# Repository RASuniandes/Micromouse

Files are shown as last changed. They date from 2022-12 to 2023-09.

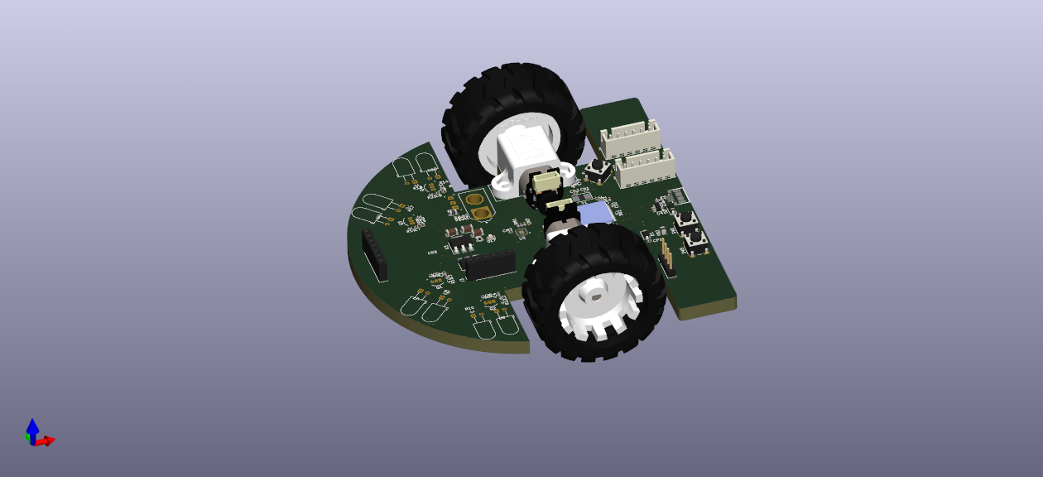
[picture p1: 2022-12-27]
Micromouse-Kicad/Micromouse-kicad.png

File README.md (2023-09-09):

<h1 align="center">RAS Uniandes  - Micromouse 🐭🧀</h1>

### The autonomous maze-solving robot:

- SoB built around the STM32F405RGT6 
  - Wall detection based on peripheral infrared sensors and ToF
  - Position and speed control using magnetic encoders for Micro Metal Motors
  - IMU aided control
  - Bluetooth support
 
- Designed using KiCad
 
- Developed in the *Universidad de Los Andes* for the *Robotics and Automation Society* Chapter of the IEEE.

## Developed by: 
<ul>
  <li>Juan Sebastián Ortega Romero(https://github.com/tadzio8425)</li>
</ul>

## To do: 
- [x] Initial research regarding the state of the art of the competition
- [x] Selection of essential components 
- [x] Initial schematic design
- [x] Altium simulations
- [x] Infrared sensors breadboard testing
- [x] Schematic revisions and corrections
- [x] PCB Design and rule check
- [x] BOM File and quote requests
- [x] Final PCB revisions
- [x] Fabrication using the services of JLCPCB
- [x] Soldering components
- [x] Unitary tests
- [x] Coding Serial, USB and Bluetooth communications
- [x] Coding sensors
- [x] Coding a general version of the FloodFill algorithm in C
- [ ] Control and PID algorithm for position and speed
- [ ] Juncture of the control algorithm and FloodFill for maze solving
- [ ] Robot calibration in a real maze
- [ ] Development of external interfaces to ease communication with the robot

## Shematic
Micromouse-kicad

## PCB Design and 3D Render

| PCB | 3D |
| --- | --- |
|  |  | 

## Robot
| Initial Assembly | Final Version |
| --- | --- |
|  |  |

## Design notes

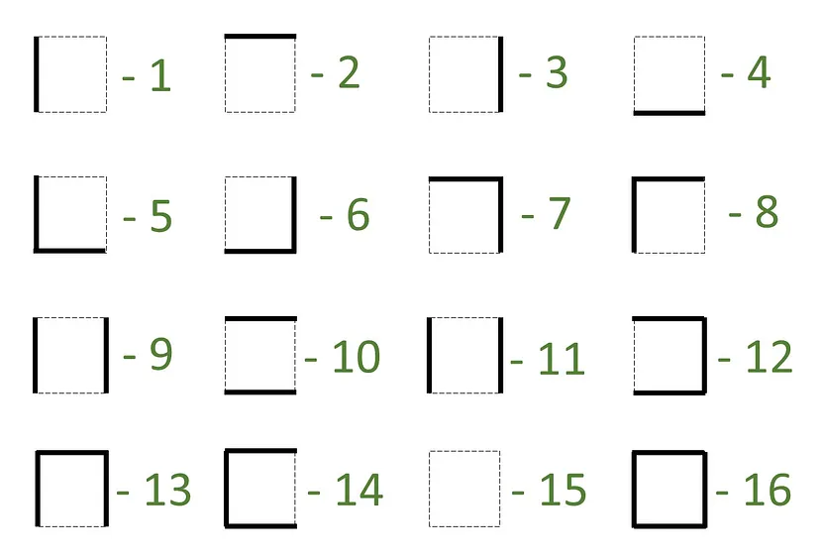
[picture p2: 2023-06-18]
Algoritmos/imgParedes.webp

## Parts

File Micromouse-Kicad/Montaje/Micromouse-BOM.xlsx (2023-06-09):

Designator | Footprint | Comment | JLCPCB Part #
RBOT1,RB2,RBOT2,RRST1,RB1 | R_0402_1005Metric | 10K | C25744
R20,R11,R19,R12 | R_0402_1005Metric | 1.5K | C25867
CRST1,CP1,CF2,CM2,CD4,CBOT1,CBOT2,CD3,CM1,CD5,CD2,CD1 | C_0402_1005Metric | 100nF | C1525
C6,CDR1,C1,C2,C5 | C_0402_1005Metric | 4.7uF | C23733
U3 | SOT-223-3_TabPin2 | AMS1117-3.3 | C6186
RU1 | R_0402_1005Metric | 1.5K | C25867
RPU1,RM1,RPU2 | R_0402_1005Metric | 4.7K | C25900
R15,R16,R8,R7,RD1 | R_0402_1005Metric | 47K | C25792
DL7 | LED_0603_1608Metric | VERDE | C72043
U5 | QFN40P300X300X95-25N | MPU-6500 | C50278
J2 | MICRO-USB-SMD_5P-P0.65-H-F_MICRO5.9MMUSB | USB_B_Micro | C393940
CD7 | C_0402_1005Metric | 2.2uF | C12530
RU2,RU3 | R_0603_1608Metric | 22 | C23345
U6 | TSSOP-16-1EP_W4.40mm | DRV8833PWPR | C50506
LF1 | L_0402_1005Metric | 27nH | C18830
CF1 | C_0402_1005Metric | 1uF | C52923
R5,R13,R14,R6 | R_0402_1005Metric | 100 | C25076
R9,R18,R10,R17 | R_0402_1005Metric | 51 | C25125
C4,C8,C7,C3 | C_0402_1005Metric | 0.1uF | C1525
CR4,CR3,CR2 | C_1206_3216Metric | 10uF | C7171
FB1,FB2 | L_0805_2012Metric | 100Ohm 100MHz | C1015
Y1 | Crystal_SMD_5032-2Pin_5.0x3.2mm | 8MHz | C115962
DL2 | LED_0603_1608Metric | AZUL | C72041
U2 | SOT-223-3_TabPin2 | AMS1117-5.0 | C6187
U4 | SOT-23-6 | SRV05-4 | C85364
R1,R4 | R_0603_1608Metric | 220 | C22962
CD6,CM3 | C_0402_1005Metric | 10nF | C15195
D2,D1 | D_SOD-123 | B5819W | C8598
RBat1 | R_0402_1005Metric | 22K | C25768
RBat2 | R_0402_1005Metric | 18K | C25762
U1 | LQFP-64_10x10mm | STM32F405RGT6 | C15742
CH1,CH2 | C_0402_1005Metric | 20pF | C1554
CR1 | C_1206_3216Metric | 0.22uF | C1857
Q1,Q2,Q3,Q4 | TO-92-3 | BS170 | C111691
J4 | AMASS_XT60-M | XT60 | C98733
J7,J6 | JST-SH-6 | SH | C160392

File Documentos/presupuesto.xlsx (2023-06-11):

Micromouse
Item | Proveedor | Unidades necesarias | Precio por unidad ($) | Precio total ($)
Encoder Magnético | Pololu (https://www.pololu.com/product/4761) | 1 | 7.95 | 7.95
Conectores JST-SH | Pololu (https://www.pololu.com/product/4765) | 2 | 2.19 | 4.38
Sujetor para motores | Pololu (https://www.pololu.com/product/1089) | 1 | 4.95 | 4.95
30:1 Motor con eje extendido | Pololu (https://www.pololu.com/product/2378) | 2 | 20.95 | 41.90
Total |  |  |  | 59.18

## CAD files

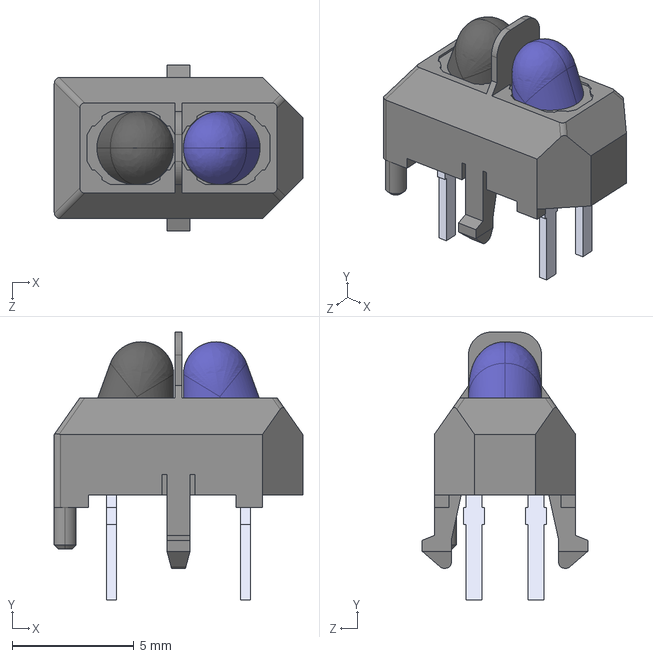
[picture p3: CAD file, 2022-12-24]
Micromouse-Kicad/Librerias/TCRT5000/TCRT5000-Footprint/TCRT5000.step
10.2 x 11.0 x 6.80 mm

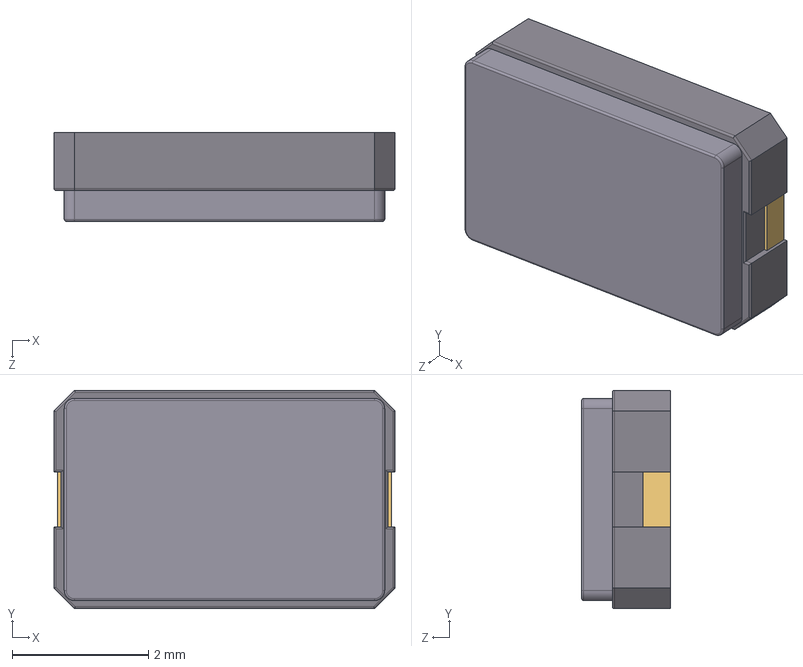
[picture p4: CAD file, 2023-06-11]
Micromouse-Kicad/Librerias/STEP/User Library-ABM3-1.STEP
5.00 x 3.20 x 1.30 mm

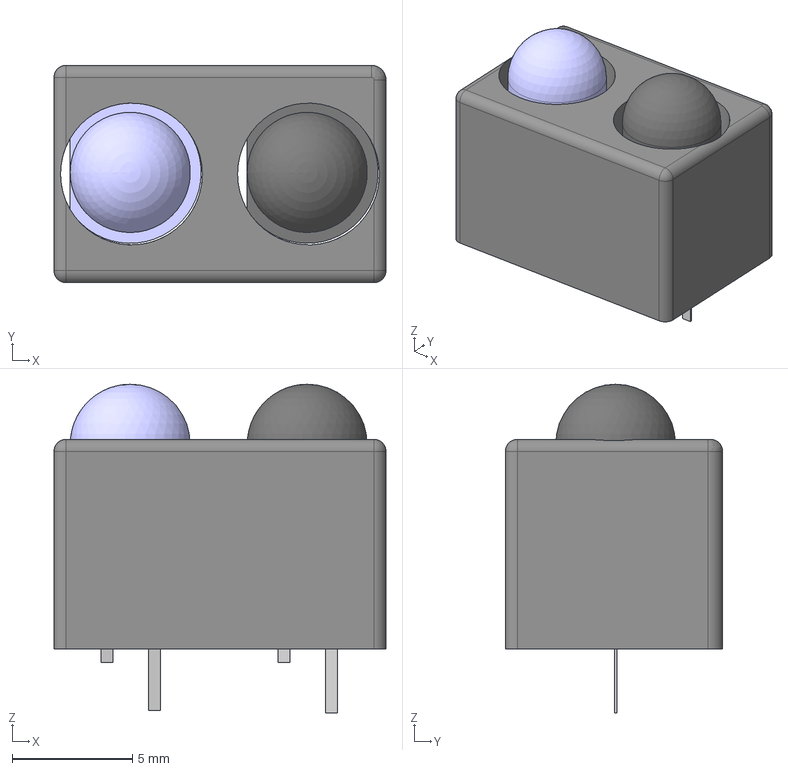
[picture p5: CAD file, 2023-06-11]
Micromouse-Kicad/Librerias/STEP/LEDcASE.step
13.8 x 9.04 x 13.7 mm
Led receptor v1
Led receptor v3

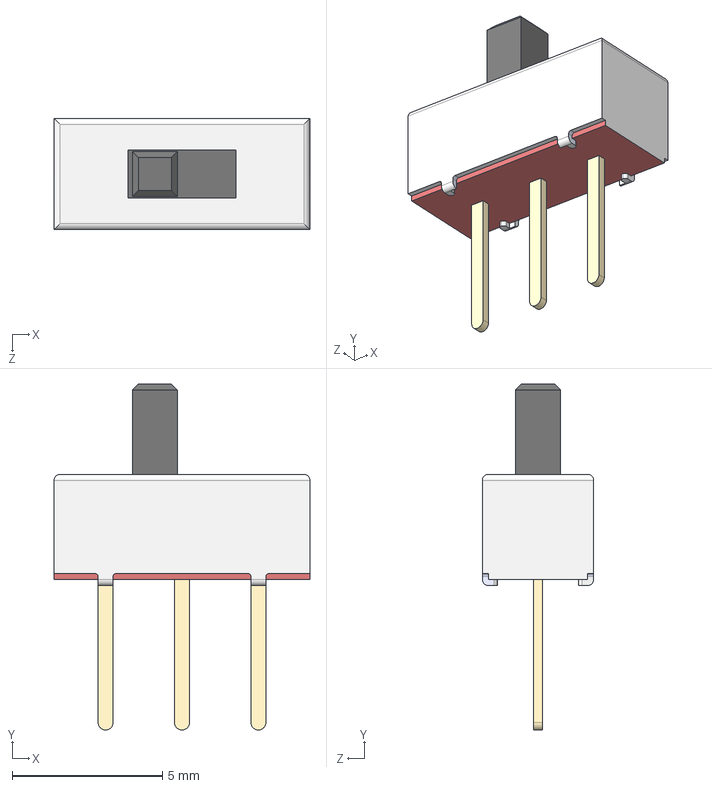
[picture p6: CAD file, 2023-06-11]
Micromouse-Kicad/Librerias/STEP/User Library-Mini Slide Switch-3Ppin-SPDT-0_3A.STEP
8.50 x 11.5 x 3.70 mm

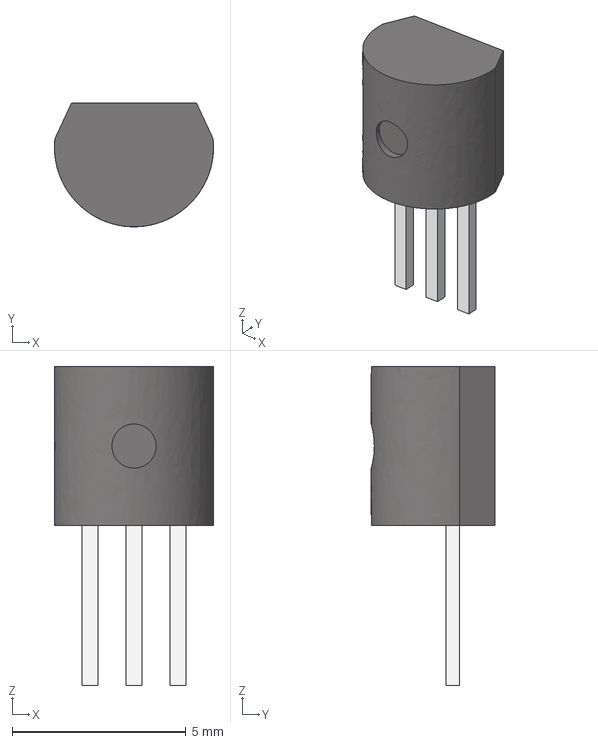
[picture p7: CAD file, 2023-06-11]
Micromouse-Kicad/Librerias/STEP/TO-92.stp
4.58 x 3.56 x 9.18 mm

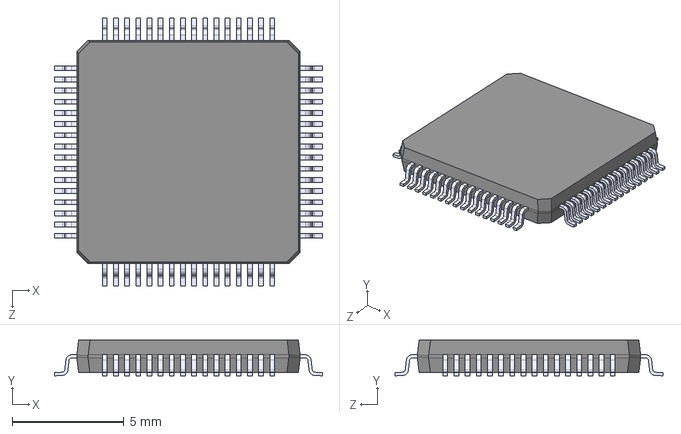
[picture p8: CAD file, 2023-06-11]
Micromouse-Kicad/Librerias/STEP/STM32F405RGT6.STEP
12.0 x 1.60 x 12.0 mm

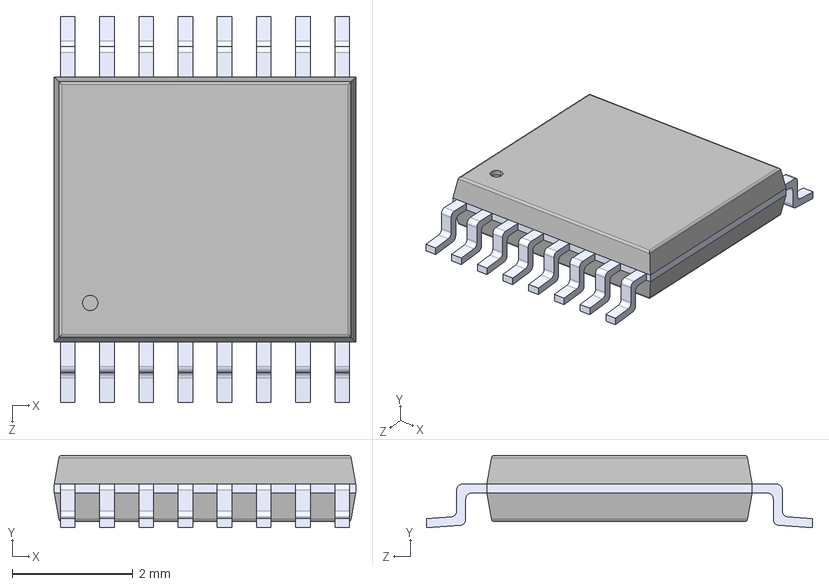
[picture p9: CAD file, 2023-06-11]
Micromouse-Kicad/Librerias/STEP/DRV8833PW.STEP
5.00 x 1.20 x 6.40 mm

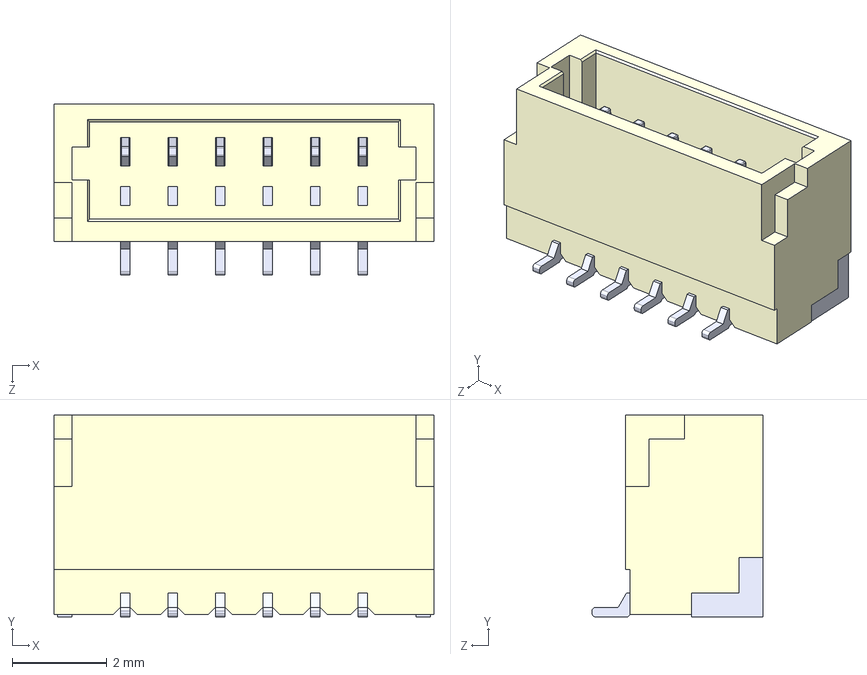
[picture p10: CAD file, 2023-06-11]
Micromouse-Kicad/Librerias/STEP/User Library-JST - BM06B-SRSS-TB (SH SERIES - 1_0mm PITCH WIRE-TO-BOARD, SMT).STEP
8.00 x 4.25 x 3.60 mm

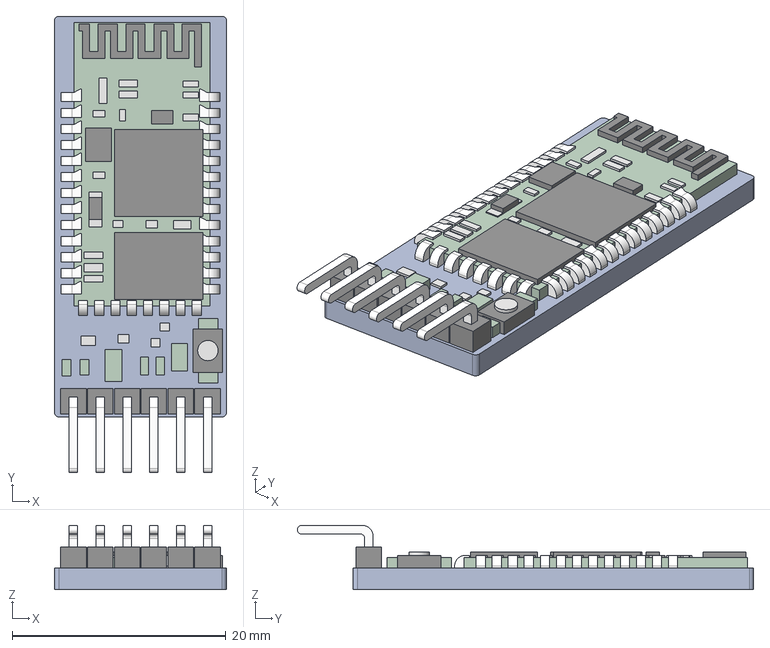
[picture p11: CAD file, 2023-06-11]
Micromouse-Kicad/Librerias/STEP/HC_05 Blue Tooth Module.stp
16.1 x 42.7 x 6.00 mm

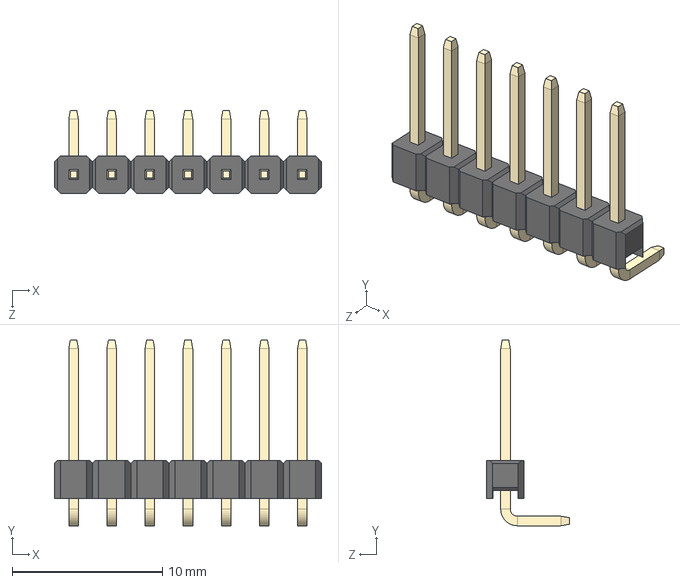
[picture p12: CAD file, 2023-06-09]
Micromouse-Kicad/Librerias/STEP/1x7 Male Pin Header Angle.STEP
17.8 x 12.4 x 5.50 mm

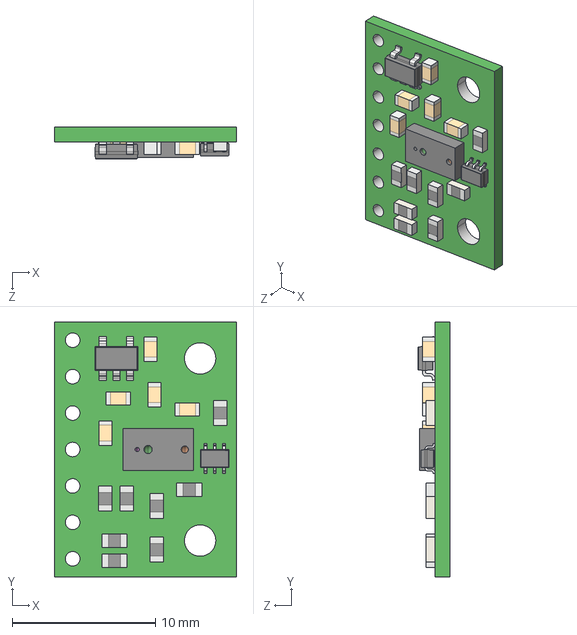
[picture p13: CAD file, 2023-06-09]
Micromouse-Kicad/Librerias/STEP/vl6180x-carrier-model.step
12.7 x 17.8 x 2.21 mm

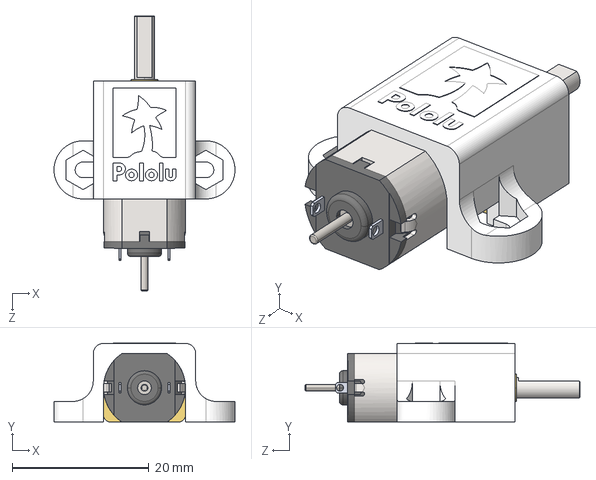
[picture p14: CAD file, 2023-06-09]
Micromouse-Kicad/Librerias/STEP/micro-metal-gearmotor-extended-with-1089-extended-bracket.step
26.5 x 11.6 x 40.2 mm

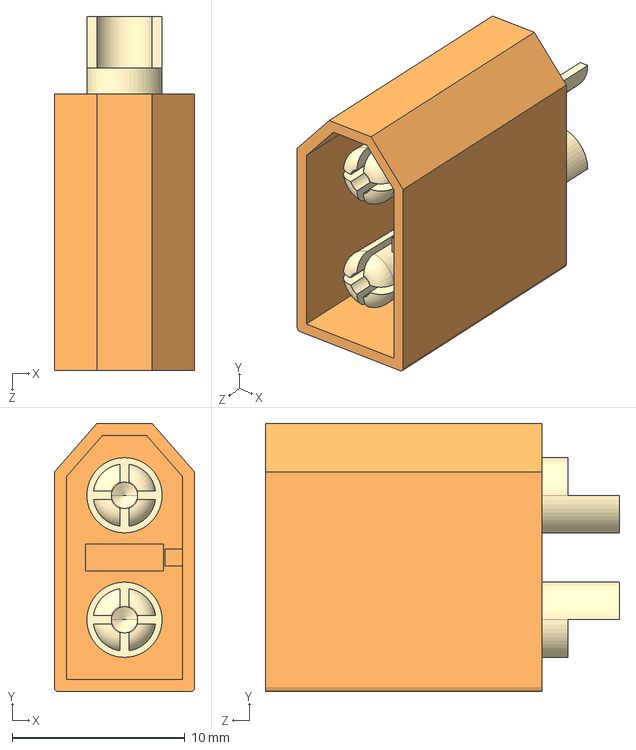
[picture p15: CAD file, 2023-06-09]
Micromouse-Kicad/Librerias/STEP/XT60-M--3DModel-STEP-56544.STEP
8.10 x 15.5 x 20.5 mm

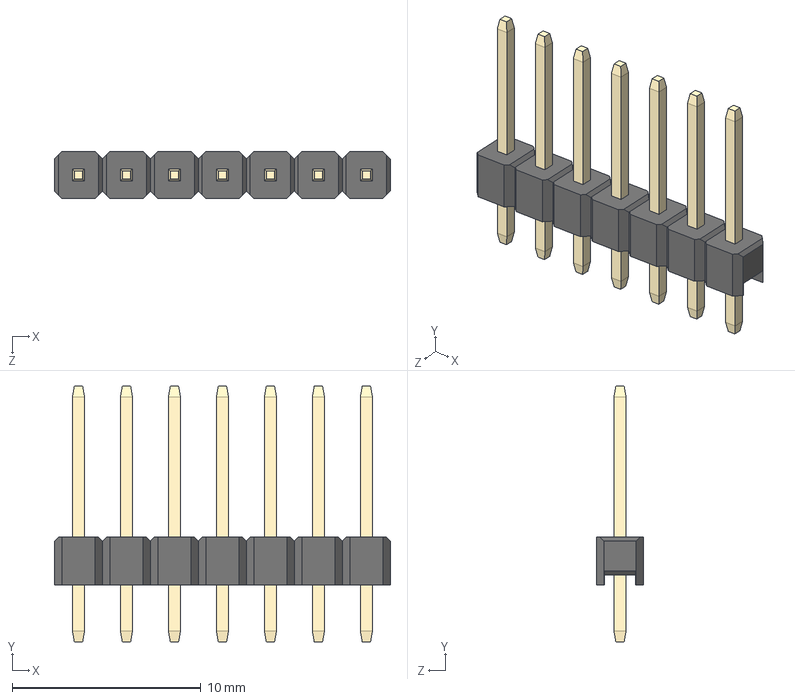
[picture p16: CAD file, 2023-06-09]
Micromouse-Kicad/Librerias/STEP/1x7 Male Pin Header.STEP
17.8 x 13.5 x 2.50 mm

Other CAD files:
Micromouse-Kicad/Librerias/STEP/Urethane_Sumo_Wheel.IGS.STP
Micromouse-Kicad/Librerias/STEP/MiniSumo_wheel.STP
Micromouse-Kicad/Librerias/STEP/magnetic-encoder-with-side-entry-connector-for-micro-metal-gearmotors.step
Micromouse-Kicad/Librerias/STEP/MPU-6500--3DModel-STEP-1.STEP
Micromouse-Kicad/Librerias/STEP/10118193-0001LF--3DModel-STEP-56544.STEP

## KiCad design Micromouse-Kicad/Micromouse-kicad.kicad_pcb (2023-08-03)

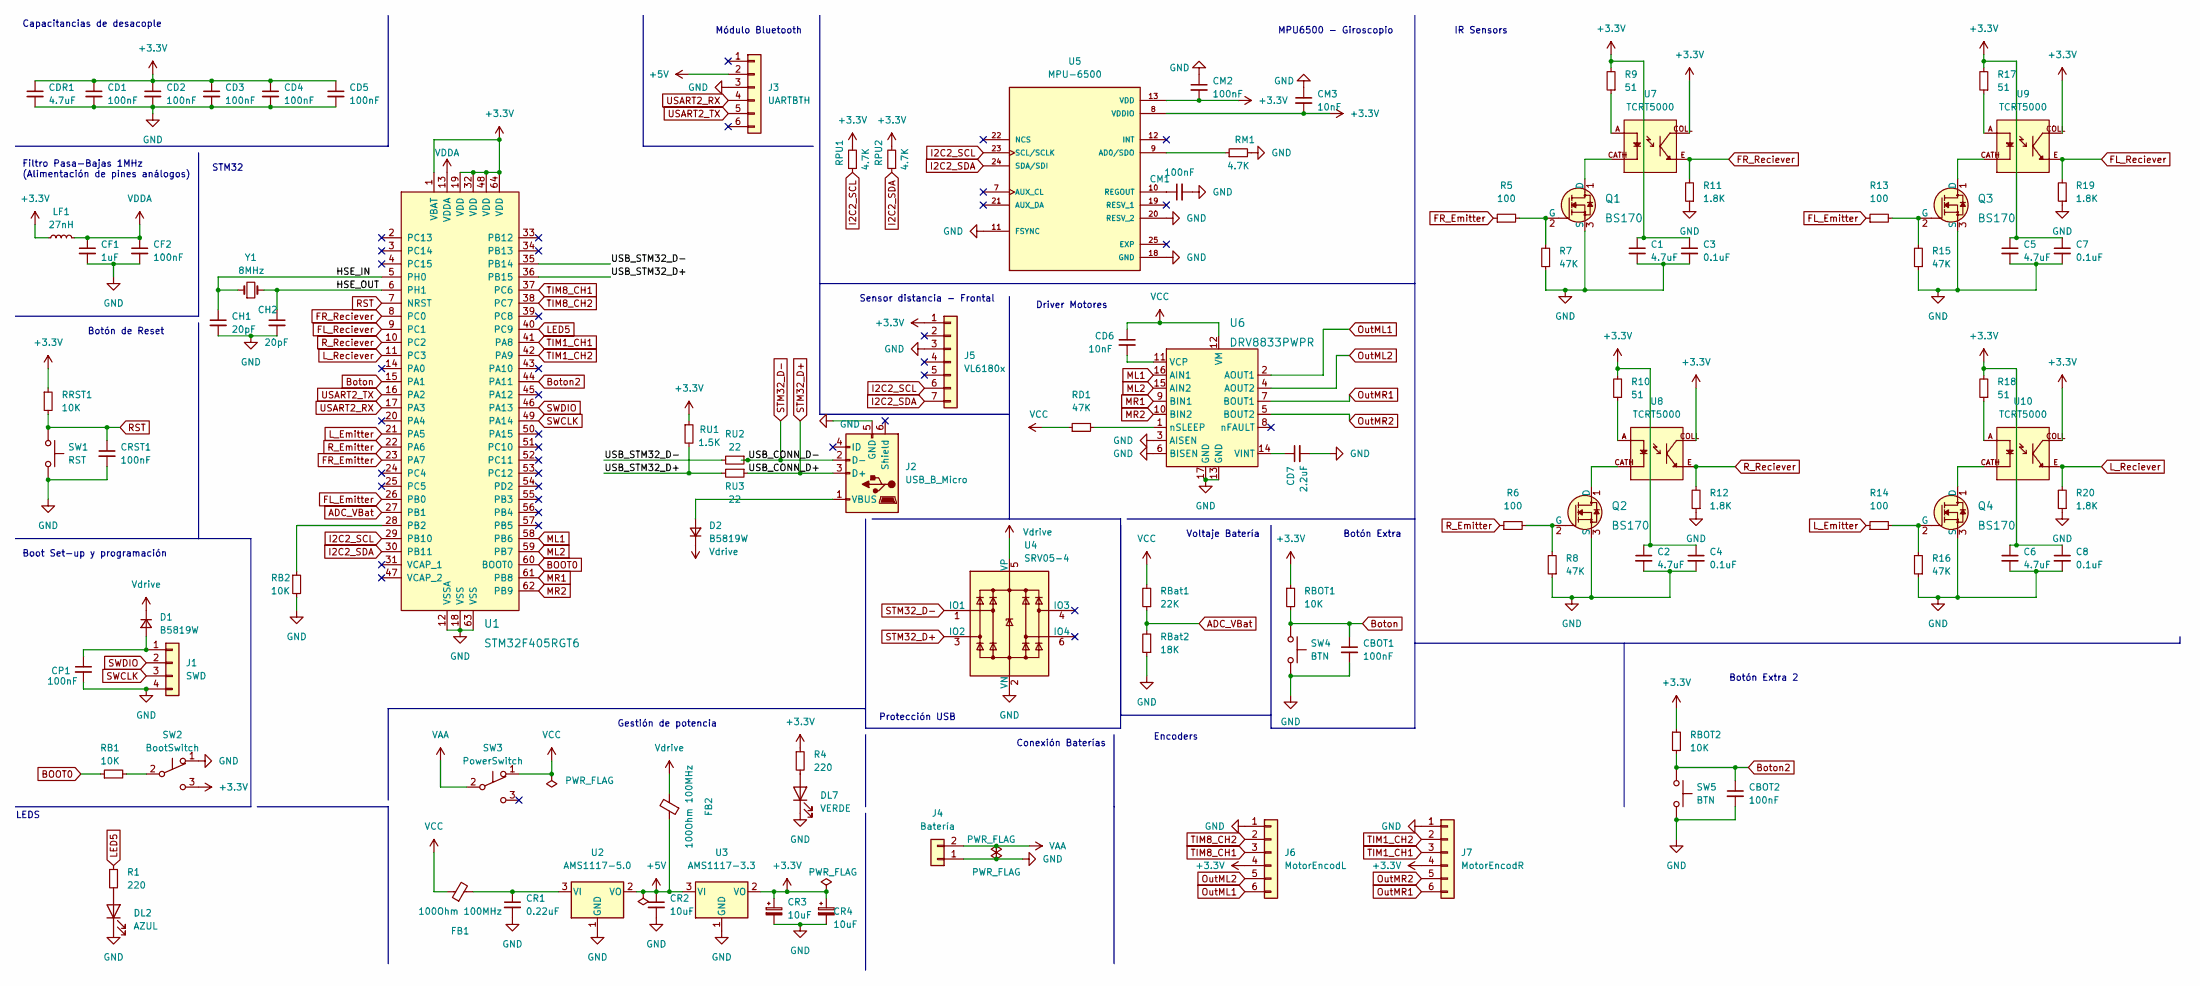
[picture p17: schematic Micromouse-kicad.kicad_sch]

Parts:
C1, C2, C5, C6: 4.7uF; C_0402_1005Metric
C3, C4, C7, C8: 0.1uF; C_0402_1005Metric
CBOT1, CBOT2: 100nF; C_0402_1005Metric
CD1, CD2, CD3, CD4, CD5: 100nF; C_0402_1005Metric
CD6: 10nF; C_0402_1005Metric
CD7: 2.2uF; C_0402_1005Metric
CDR1: 4.7uF; C_0402_1005Metric
CF1: 1uF; C_0402_1005Metric
CF2: 100nF; C_0402_1005Metric
CH1, CH2: 20pF; C_0402_1005Metric
CM1, CM2: 100nF; C_0402_1005Metric
CM3: 10nF; C_0402_1005Metric
CP1: 100nF; C_0402_1005Metric
CR1: 0.22uF; C_1206_3216Metric
CR2, CR3, CR4: 10uF; C_1206_3216Metric
CRST1: 100nF; C_0402_1005Metric
D1, D2: B5819W; D_SOD-123
DL2: AZUL; LED_0603_1608Metric
DL7: VERDE; LED_0603_1608Metric
FB1, FB2: 100Ohm 100MHz; L_0805_2012Metric
J1: SWD; PinHeader_1x04_P2.54mm_Vertical
J2: USB_B_Micro; MICRO-USB-SMD_5P-P0.65-H-F_MICRO5.9MMUSB
J3: UARTBTH; PinSocket_1x06_P2.54mm_Vertical
J4: Batería; AMASS_XT60-M
J5: VL6180x; PinSocket_1x07_P2.54mm_Vertical
J6: MotorEncodL; JST_SH_BM06B-SRSS-TB_1x06-1MP_P1.00mm_Vertical
J7: MotorEncodR; JST_SH_BM06B-SRSS-TB_1x06-1MP_P1.00mm_Vertical
LF1: 27nH; L_0402_1005Metric
Q1, Q2, Q3, Q4: BS170; TO-92-3; MPN BS170; Digi-Key_PN BS170-ND
R1, R4: 220; R_0603_1608Metric
R5, R6, R13, R14: 100; R_0402_1005Metric
R7, R8, R15, R16: 47K; R_0402_1005Metric
R9, R10, R17, R18: 51; R_0402_1005Metric
R11, R12, R19, R20: 1.8K; R_0402_1005Metric
RB1, RB2: 10K; R_0402_1005Metric
RBOT1, RBOT2: 10K; R_0402_1005Metric
RBat1: 22K; R_0402_1005Metric
RBat2: 18K; R_0402_1005Metric
RD1: 47K; R_0402_1005Metric
RM1: 4.7K; R_0402_1005Metric
RPU1, RPU2: 4.7K; R_0402_1005Metric
RRST1: 10K; R_0402_1005Metric
RU1: 1.5K; R_0402_1005Metric
RU2, RU3: 22; R_0603_1608Metric
SW1: RST; SW_PUSH_6mm_H5mm
SW2: BootSwitch; Switch_Slide
SW3: PowerSwitch; Switch_Slide
SW4, SW5: BTN; SW_PUSH_6mm_H5mm
U1: STM32F405RGT6; LQFP-64_10x10mm; MPN STM32F405RGT6; Digi-Key_PN 497-11767-ND
U2: AMS1117-5.0; SOT-223-3_TabPin2
U3: AMS1117-3.3; SOT-223-3_TabPin2
U4: SRV05-4; SOT-23-6
U5: MPU-6500; QFN40P300X300X95-25N; PARTREV 1.3
U6: DRV8833PWPR; TSSOP-16-1EP_W4.40mm; MPN DRV8833PWPR; Digi-Key_PN 296-29434-1-ND
U7, U8, U9, U10: TCRT5000; OPTO_TCRT5000; PARTREV 1.7
Y1: 8MHz; Crystal_SMD_5032-2Pin_5.0x3.2mm

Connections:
+3.3V: C1.1, C2.1, C3.1, C4.1, C5.1, C6.1, C7.1, C8.1, CD1.1, CD2.1, CD3.1, CD4.1, CD5.1, CDR1.1, CM2.2, CM3.2, CR3.1, CR4.1, J5.1, J6.4, J7.4, LF1.1, R4.1, R9.2, R10.2, R17.2, R18.2, RBOT1.1, RBOT2.1, RPU1.2, RPU2.2, RRST1.1, RU1.1, SW2.3 (C), U1.1 (VBAT), U1.19 (VDD), U1.32 (VDD), U1.48 (VDD), U1.64 (VDD), U3.2 (VO), U5.8 (VDDIO), U5.13 (VDD), U7.COLL, U8.COLL, U9.COLL, U10.COLL
+5V: CR2.1, FB2.1, J3.2, U2.2 (VO), U3.3 (VI)
/HSE_IN: CH1.1, U1.5 (PH0), Y1.1
/HSE_OUT: CH2.1, U1.6 (PH1), Y1.2
/USB_STM32_D+: RU1.2, RU3.2, U1.36 (PB15)
/USB_STM32_D-: RU2.2, U1.35 (PB14)
ADC_VBat: RBat1.1, RBat2.2, U1.27 (PB1)
BOOT0: RB1.1, U1.60 (BOOT0)
Boton: CBOT1.1, RBOT1.2, SW4.1, U1.15 (PA1)
Boton2: CBOT2.1, RBOT2.2, SW5.1, U1.44 (PA11)
FL_Emitter: R13.1, U1.26 (PB0)
FL_Reciever: R19.2, U1.9 (PC1), U9.E
FR_Emitter: R5.1, U1.23 (PA7)
FR_Reciever: R11.2, U1.8 (PC0), U7.E
GND: C1.2, C2.2, C3.2, C4.2, C5.2, C6.2, C7.2, C8.2, CBOT1.2, CBOT2.2, CD1.2, CD2.2, CD3.2, CD4.2, CD5.2, CD7.2, CDR1.2, CF1.2, CF2.2, CH1.2, CH2.2, CM1.2, CM2.1, CM3.1, CP1.2, CR1.2, CR2.2, CR3.2, CR4.2, CRST1.2, DL2.1 (K), DL7.1 (K), J1.4, J2.5 (GND), J3.3, J4.1, J5.3, J6.1, J7.1, Q1.3 (S), Q2.3 (S), Q3.3 (S), Q4.3 (S), R7.1, R8.1, R11.1, R12.1, R15.1, R16.1, R19.1, R20.1, RB2.2, RBat2.1, RM1.2, SW1.2, SW2.1 (A), SW4.2, SW5.2, U1.12 (VSSA), U1.18 (VSS), U1.63 (VSS), U2.1 (GND), U3.1 (GND), U4.2 (VN), U5.11 (FSYNC), U5.18 (GND), U5.20 (RESV_2), U6.3 (AISEN), U6.6 (BISEN), U6.13 (GND), U6.17 (GND)
I2C2_SCL: J5.6, RPU1.1, U1.29 (PB10), U5.23 (SCL/SCLK)
I2C2_SDA: J5.7, RPU2.1, U1.30 (PB11), U5.24 (SDA/SDI)
LED5: R1.1, U1.40 (PC9)
L_Emitter: R14.1, U1.21 (PA5)
L_Reciever: R20.2, U1.11 (PC3), U10.E
ML1: U1.58 (PB6), U6.16 (AIN1)
ML2: U1.59 (PB7), U6.15 (AIN2)
MR1: U1.61 (PB8), U6.9 (BIN1)
MR2: U1.62 (PB9), U6.10 (BIN2)
unnamed: CP1.1, D1.2 (A), J1.1
unnamed: D2.2 (A), J2.1 (VBUS)
unnamed: DL2.2 (A), R1.2
unnamed: DL7.2 (A), R4.2
unnamed: Q1.1 (D), U7.CATH
unnamed: Q1.2 (G), R5.2, R7.2
unnamed: Q2.1 (D), U8.CATH
unnamed: Q2.2 (G), R6.2, R8.2
unnamed: Q3.1 (D), U9.CATH
unnamed: Q3.2 (G), R13.2, R15.2
unnamed: Q4.1 (D), U10.CATH
unnamed: Q4.2 (G), R14.2, R16.2
unnamed: R9.1, U7.A
unnamed: R10.1, U8.A
unnamed: R17.1, U9.A
unnamed: R18.1, U10.A
unnamed: RB1.2, SW2.2 (B)
unnamed: RB2.1, U1.28 (PB2)
unnamed: CR1.1, FB1.2, U2.3 (VI)
unnamed: RM1.1, U5.9 (AD0/SDO)
unnamed: CM1.1, U5.10 (REGOUT)
unnamed: CD6.2, U6.11 (VCP)
unnamed: CD7.1, U6.14 (VINT)
unnamed: RD1.2, U6.1 (nSLEEP)
OutML1: J6.6, U6.2 (AOUT1)
OutML2: J6.5, U6.4 (AOUT2)
OutMR1: J7.6, U6.7 (BOUT1)
OutMR2: J7.5, U6.5 (BOUT2)
RST: CRST1.1, RRST1.2, SW1.1, U1.7 (NRST)
R_Emitter: R6.1, U1.22 (PA6)
R_Reciever: R12.2, U1.10 (PC2), U8.E
STM32_D+: J2.3 (D+), RU3.1, U4.3 (IO2)
STM32_D-: J2.2 (D-), RU2.1, U4.1 (IO1)
SWCLK: J1.3, U1.49 (PA14)
SWDIO: J1.2, U1.46 (PA13)
TIM1_CH1: J7.3, U1.41 (PA8)
TIM1_CH2: J7.2, U1.42 (PA9)
TIM8_CH1: J6.3, U1.37 (PC6)
TIM8_CH2: J6.2, U1.38 (PC7)
USART2_RX: J3.4, U1.17 (PA3)
USART2_TX: J3.5, U1.16 (PA2)
VAA: J4.2, SW3.2 (B)
VCC: CD6.1, FB1.1, RBat1.2, RD1.1, SW3.1 (A), U6.12 (VM)
VDDA: CF1.1, CF2.1, LF1.2, U1.13 (VDDA)
Vdrive: D1.1 (K), D2.1 (K), FB2.2, U4.5 (VP)

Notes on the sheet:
Protección USB
Voltaje Batería
LEDS
Gestión de potencia
Conexión Baterías
MPU6500 - Giroscopio
Botón Extra
STM32
IR Sensors
Módulo Bluetooth
Botón de Reset
Encoders
Botón Extra 2
Driver Motores
Capacitancias de desacople
Boot Set-up y programación
Filtro Pasa-Bajas 1MHz (Alimentación de pines análogos)
Sensor distancia - Frontal

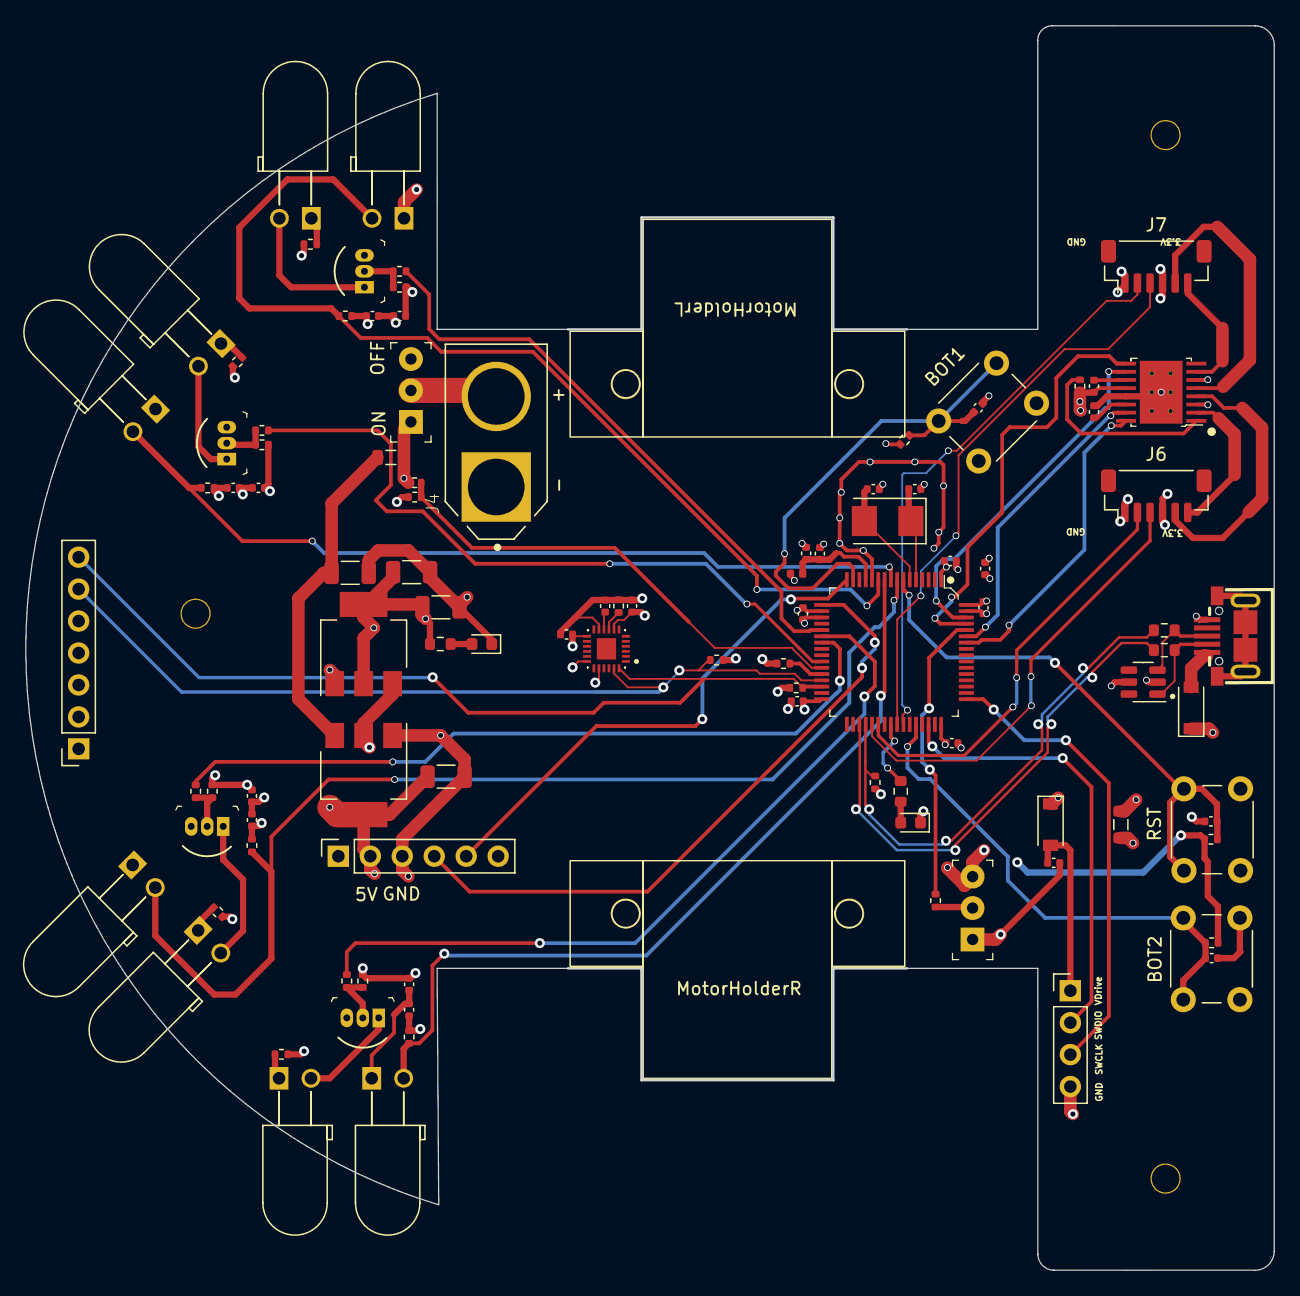
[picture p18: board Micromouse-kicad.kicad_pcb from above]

Board: 4 copper layers, 99.2 x 98.9 mm, 99 parts (0 on the bottom side), 69 nets.

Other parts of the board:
MotorHolderL: Pololu; MotorHolder
MotorHolderR: Pololu; MotorHolder

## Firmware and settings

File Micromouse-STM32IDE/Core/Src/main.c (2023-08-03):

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
/* Includes ------------------------------------------------------------------*/
#include "main.h"
#include "usb_device.h"

/* USER CODE BEGIN Includes */
#include "irs.h"
#include "motors.h"
#include "encoder.h"
#include "usb_device.h"
#include "string.h"
#include "usbd_cdc_if.h"
#include "mpu6500.h"
#include "delay.h"
#include "vl6180x.h"
#include "moving_average.h"
#include "pid.h"

/* USER CODE END Includes */

ADC_HandleTypeDef hadc1;
ADC_HandleTypeDef hadc2;
DMA_HandleTypeDef hdma_adc1;

I2C_HandleTypeDef hi2c2;

TIM_HandleTypeDef htim1;
TIM_HandleTypeDef htim4;
TIM_HandleTypeDef htim8;

UART_HandleTypeDef huart2;
DMA_HandleTypeDef hdma_usart2_tx;

/* USER CODE BEGIN PV */
encoder_instance enc_right;
encoder_instance enc_left;

float* mpu_data;


int16_t left_IR;
int16_t right_IR;
int16_t front_left_IR;
int16_t front_right_IR;
uint8_t tof;
float vBat;

uint8_t init_vl6180;


//BUFFERS USB
uint8_t usb_data[300];
char text_buffer[20];
uint8_t recieve_buffer[64];


//BUFFERS UART
#define BUFFER_LEN 64
uint8_t RX_BUFFER[BUFFER_LEN] = {0};
uint8_t recieve_index = 0;



//MOVING AVERAGE FILTER
mov_aver_inst  filter_speedMR;
mov_aver_inst  filter_speedML;


//Velocidad Motores RPM (FINAL)
double vel_rightM_RPM;
double vel_leftM_RPM;
double speedDifference;

double ref_rightM_RPM = 500;
double ref_leftM_RPM = 500;

double speedMR_output;
double speedML_output;
double speedDifference_output;

uint8_t enable_motors = 0;

//INSTANCIAS PID
PID_TypeDef speedMR_PID;
PID_TypeDef speedML_PID;
PID_TypeDef speedDifference_PID;

/* USER CODE END PV */

void SystemClock_Config(void);
static void MX_GPIO_Init(void);
static void MX_DMA_Init(void);
static void MX_TIM4_Init(void);
static void MX_TIM1_Init(void);
static void MX_TIM8_Init(void);
static void MX_I2C2_Init(void);
static void MX_ADC1_Init(void);
static void MX_ADC2_Init(void);
static void MX_USART2_UART_Init(void);
/* USER CODE BEGIN PFP */
extern uint8_t CDC_Transmit_HS(uint8_t* Buf, uint16_t Len);

/* USER CODE END PFP */

/**
  * @brief  The application entry point.
  * @retval int
  */
int main(void)
{
  /* MCU Configuration--------------------------------------------------------*/

  /* Reset of all peripherals, Initializes the Flash interface and the Systick. */
+  HAL_Init();

  /* USER CODE BEGIN Init */
  Delay_Init();

  /* USER CODE END Init */

  /* Configure the system clock */
  SystemClock_Config();

  /* Initialize all configured peripherals */
  MX_GPIO_Init();
  MX_DMA_Init();
  MX_TIM4_Init();
  MX_TIM1_Init();
  MX_TIM8_Init();
  MX_USB_DEVICE_Init();
  MX_I2C2_Init();
  MX_ADC1_Init();
  MX_ADC2_Init();
  MX_USART2_UART_Init();
  /* USER CODE BEGIN 2 */




  //Inicialización I2C



  // Timers PWM - Motores
  HAL_TIM_PWM_Start(&htim4, TIM_CHANNEL_1); //L_Emitter
  HAL_TIM_PWM_Start(&htim4, TIM_CHANNEL_2); //R_Emitter
  HAL_TIM_PWM_Start(&htim4, TIM_CHANNEL_3); //FR_Emitter
  HAL_TIM_PWM_Start(&htim4, TIM_CHANNEL_4); //FL_Emitter

  // Timers ENCODERS
  HAL_TIM_Encoder_Start(&htim1, TIM_CHANNEL_ALL);
  HAL_TIM_Encoder_Start(&htim8, TIM_CHANNEL_ALL);

  //MPU6500
  mpu6500_init();



  // vl6180x
  //VL6180X_Init(&hi2c2);


  //Inicialización PID
  PID(&speedMR_PID, &enc_right.position_mm, &speedMR_output, &ref_rightM_RPM, 0.008, 0.0001,  0.0004, _PID_P_ON_E, _PID_CD_DIRECT);
  PID_SetMode(&speedMR_PID, _PID_MODE_AUTOMATIC);
  PID_SetSampleTime(&speedMR_PID, 1);
  PID_SetOutputLimits(&speedMR_PID, 0, 1);

  PID(&speedML_PID, &enc_left.position_mm, &speedML_output,  &ref_leftM_RPM, 0.008, 0.0001, 0.0004, _PID_P_ON_E, _PID_CD_DIRECT);
  PID_SetMode(&speedML_PID, _PID_MODE_AUTOMATIC);
  PID_SetSampleTime(&speedML_PID, 1);
  PID_SetOutputLimits(&speedML_PID, 0, 1);

  double zero = 0;
  PID(&speedDifference_PID, &speedDifference, &speedDifference_output,  &zero, 0.008, 0.0001, 0.0004, _PID_P_ON_E, _PID_CD_DIRECT);
  PID_SetMode(&speedDifference_PID, _PID_MODE_AUTOMATIC);
  PID_SetSampleTime(&speedDifference_PID, 1);
  PID_SetOutputLimits(&speedDifference_PID, 0, 1);

  /* USER CODE END 2 */

  /* Infinite loop */
  /* USER CODE BEGIN WHILE */
  while (1)
  {
    /* USER CODE END WHILE */

    /* USER CODE BEGIN 3 */
	HAL_GPIO_TogglePin(BLUE_GPIO_Port, BLUE_Pin);


	/*Lectura IR*/
	right_IR = readIR(IR_RIGHT);
	left_IR = readIR(IR_LEFT);//
	front_left_IR = readIR(IR_FRONT_LEFT);
	front_right_IR = readIR(IR_FRONT_RIGHT);

	/*Lectura del vl6180x*/
	//tof = VL6180X_readRange();

	//Lectura del MPU
	mpu_data = mpu6500_read();


	//Lectura VOltaje Bateria
	HAL_ADC_Start(&hadc2);
	vBat = HAL_ADC_GetValue(&hadc2) * (7.76/4095.0);


	//Pruebas motores
	if(HAL_GPIO_ReadPin(BOTON1_GPIO_Port, BOTON1_Pin) == 0){
		 ref_rightM_RPM = 360;
		 ref_leftM_RPM = 360;

		 enable_motors = 1;
	}


	//USB DATA
	print_sensorData();
	//CDC_Transmit_HS(usb_data, strlen(usb_data));
	HAL_UART_Transmit(&huart2, usb_data, strlen (usb_data), 100);
	memset(usb_data, '\0', 300);



  }
  /* USER CODE END 3 */
}

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
/* USER CODE BEGIN 4 */
ADC_HandleTypeDef* Get_HADC1_Ptr(void)
{
    return &hadc1;
}

void print_RMotorSpeed(){
	sprintf(text_buffer, "\n%f, ", vel_rightM_RPM);
	strncat(usb_data, text_buffer, strlen(text_buffer));
	sprintf(text_buffer, "%d", HAL_GetTick());
	strncat(usb_data, text_buffer, strlen(text_buffer));
}


void print_sensorData(){
	sprintf(text_buffer, "\n\n L: %d, ", left_IR);
	strncat(usb_data, text_buffer, strlen(text_buffer));
	sprintf(text_buffer, "FL: %d, ", front_left_IR);
	strncat(usb_data, text_buffer, strlen(text_buffer));
	sprintf(text_buffer, "FR: %d, ", front_right_IR);
	strncat(usb_data, text_buffer, strlen(text_buffer));
	sprintf(text_buffer, "R: %d, ", right_IR);
	strncat(usb_data, text_buffer, strlen(text_buffer));
	sprintf(text_buffer, "F: %d \n", tof);
	strncat(usb_data, text_buffer, strlen(text_buffer));

	//DATA - MPU
	sprintf(text_buffer, "AX: %f, ",  mpu_data[0]);
	strncat(usb_data, text_buffer, strlen(text_buffer));
	sprintf(text_buffer, "AY: %f, ", mpu_data[1]);
	strncat(usb_data, text_buffer, strlen(text_buffer));
	sprintf(text_buffer, "AZ: %f, ", mpu_data[2]);
	strncat(usb_data, text_buffer, strlen(text_buffer));

	sprintf(text_buffer, "T: %f \n", mpu_data[3]);
	strncat(usb_data, text_buffer, strlen(text_buffer));

	sprintf(text_buffer, "GX: %f, ", mpu_data[4]);
	strncat(usb_data, text_buffer, strlen(text_buffer));
	sprintf(text_buffer, "GY: %f, ", mpu_data[5]);
	strncat(usb_data, text_buffer, strlen(text_buffer));
	sprintf(text_buffer, "GZ: %f, ", mpu_data[6]);
	strncat(usb_data, text_buffer, strlen(text_buffer));

	//Data Batería
	sprintf(text_buffer, "\n vBat: %f ", vBat);
	strncat(usb_data, text_buffer, strlen(text_buffer));
}



/* USER CODE END 4 */
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


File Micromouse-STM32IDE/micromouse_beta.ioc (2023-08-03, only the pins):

Mcu.UserName=STM32F405RGTx
PA1.GPIO_Label=BOTON1
PA1.Signal=GPIO_Input
PA11.GPIO_Label=BOTON2
PA11.Signal=GPIO_Input
PA13.Signal=SYS_JTMS-SWDIO
PA14.Signal=SYS_JTCK-SWCLK
PA2.Signal=USART2_TX
PA3.Signal=USART2_RX
PA5.GPIO_Label=R_Emitter
PA5.Signal=GPIO_Output
PA6.GPIO_Label=L_Emitter
PA6.Signal=GPIO_Output
PA7.GPIO_Label=FL_Emitter
PA7.Signal=GPIO_Output
PA8.Signal=S_TIM1_CH1
PA9.Signal=S_TIM1_CH2
PB0.GPIO_Label=FR_Emitter
PB0.Signal=GPIO_Output
PB1.GPIO_Label=vBat
PB1.Signal=ADCx_IN9
PB10.Signal=I2C2_SCL
PB11.Signal=I2C2_SDA
PB14.Signal=USB_OTG_HS_DM
PB15.Signal=USB_OTG_HS_DP
PB6.Signal=S_TIM4_CH1
PB7.Signal=S_TIM4_CH2
PB8.Signal=S_TIM4_CH3
PB9.Signal=S_TIM4_CH4
PC0.GPIO_Label=FL_Reciever
PC0.Signal=ADCx_IN10
PC1.GPIO_Label=FR_Reciever
PC1.Signal=ADCx_IN11
PC2.GPIO_Label=L_Reciever
PC2.Signal=ADCx_IN12
PC3.GPIO_Label=R_Reciever
PC3.Signal=ADCx_IN13
PC6.Signal=S_TIM8_CH1
PC7.Signal=S_TIM8_CH2
PC9.GPIO_Label=BLUE
PC9.Signal=GPIO_Output
PH0-OSC_IN.Signal=RCC_OSC_IN
PH1-OSC_OUT.Signal=RCC_OSC_OUT

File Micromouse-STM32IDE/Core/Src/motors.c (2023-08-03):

/*
 * motors.c
 */

#include "motors.h"

/*
 * This function should return PWM_MAX if pwm > PWM_MAX, -PWM_MAX if pwm < -PWM_MAX, and pwm otherwise.
 */
float limitPWM(float pwm) {
	if (pwm > PWM_MAX) {
		return PWM_MAX;
	} else if (pwm < -PWM_MAX) {
		return -PWM_MAX;
	} else {
		return pwm;
	}
}

/*
 * This function controls the left motor speed and direction. We do this by setting the timer pulse value for the appropriate channel.
 * All our H-bridge inputs use timer 4. TIM4->CCRX = (uint32_t) (limitPWM(pwm) * MAX_TIMER_COUNTS) sets the pulse value for channel x.
 * For the left motor, setting channel 3 makes the wheel spin forward and setting channel 4 makes the wheel spin backwards.
 *
 * The parameter pwm is a value between 0 and 1, representing the percentage of maximum speed to turn the motor. e.g. 0.5 is half speed.
 *
 * IMPORTANT: NEVER SET BOTH THE FORWARD AND BACKWARD CHANNELS TO NON-ZERO VALUES AT THE SAME TIME. As mentioned in lecture, this can
 * destroy your h-bridge. When setting a channel, always set the other channel to zero first.
 *
 * Implement this function to make the left wheel spin forwards when pwm is >= 0, and spin backwards when pwm < 0.
 */
void setMotorLPWM(float pwm) {
	if (pwm >= 0) {
		TIM4->CCR2 = 0;
		TIM4->CCR1 = (uint32_t) (limitPWM(pwm) * MAX_TIMER_COUNTS);
	} else {
		TIM4->CCR1 = 0;
		TIM4->CCR2 = (uint32_t) (limitPWM(pwm) * -MAX_TIMER_COUNTS);
	}
}

/*
 * This function controls the right motor speed and direction. We do this by setting the timer pulse value for the appropriate channel.
 * All our H-bridge inputs use timer 4. TIM4->CCRX = (uint32_t) (limitPWM(pwm) * MAX_TIMER_COUNTS) sets the pulse value for channel x.
 * For the right motor, setting channel 1 makes the wheel spin forward and setting channel 2 makes the wheel spin backwards.
 *
 * The parameter pwm is a value between 0 and 1, representing the percentage of maximum speed to turn the motor. e.g. 0.5 is half speed.
 *
 * IMPORTANT: NEVER SET BOTH THE FORWARD AND BACKWARD CHANNELS TO NON-ZERO VALUES AT THE SAME TIME. As mentioned in lecture, this can
 * destroy your h-bridge. When setting a channel, always set the other channel to zero first.
 *
 * Implement this function to make the right wheel spin forwards when pwm is >= 0, and spin backwards when pwm < 0.
 */
void setMotorRPWM(float pwm) {
	if (pwm >= 0) {
		TIM4->CCR3 = 0;
		TIM4->CCR4 = (uint32_t) (limitPWM(pwm) * MAX_TIMER_COUNTS);
	} else {
		TIM4->CCR4 = 0;
		TIM4->CCR3 = (uint32_t) (limitPWM(pwm) * -MAX_TIMER_COUNTS);
	}
}

/*
 * Using the two previous setMotorPWM functions, implement resetMotors to set the PWM for both wheels to zero, effectively stopping them.
 */
void resetMotors() {
	setMotorLPWM(0);
	setMotorRPWM(0);
}

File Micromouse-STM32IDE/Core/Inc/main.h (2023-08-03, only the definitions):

#define FL_Reciever_Pin GPIO_PIN_0
#define FL_Reciever_GPIO_Port GPIOC
#define FR_Reciever_Pin GPIO_PIN_1
#define FR_Reciever_GPIO_Port GPIOC
#define L_Reciever_Pin GPIO_PIN_2
#define L_Reciever_GPIO_Port GPIOC
#define R_Reciever_Pin GPIO_PIN_3
#define R_Reciever_GPIO_Port GPIOC
#define BOTON1_Pin GPIO_PIN_1
#define BOTON1_GPIO_Port GPIOA
#define R_Emitter_Pin GPIO_PIN_5
#define R_Emitter_GPIO_Port GPIOA
#define L_Emitter_Pin GPIO_PIN_6
#define L_Emitter_GPIO_Port GPIOA
#define FL_Emitter_Pin GPIO_PIN_7
#define FL_Emitter_GPIO_Port GPIOA
#define FR_Emitter_Pin GPIO_PIN_0
#define FR_Emitter_GPIO_Port GPIOB
#define vBat_Pin GPIO_PIN_1
#define vBat_GPIO_Port GPIOB
#define BLUE_Pin GPIO_PIN_9
#define BLUE_GPIO_Port GPIOC
#define BOTON2_Pin GPIO_PIN_11
#define BOTON2_GPIO_Port GPIOA

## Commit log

2022-12-24 Avance esquemático - STM32, MPU6500, Driver Motores
    [MPU-6500.step, Micromouse-kicad.kicad_pcb, Micromouse-kicad.kicad_sch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]
2022-12-24 Esquemático con componentes básicos
    [Micromouse-kicad.kicad_sch, TCRT5000.step]
2022-12-24 Huellas agregadas
    [Micromouse-kicad.kicad_pcb, Micromouse-kicad.kicad_sch]
2022-12-26 Avance PCB - Forma y motores
    [Micromouse-kicad.kicad_pcb]
2022-12-27 Motores routeados
    [Micromouse-kicad.kicad_pcb, Micromouse-kicad.kicad_sch]
2022-12-27 MPU6500 routeado
    [Micromouse-kicad.kicad_pcb]
2022-12-27 Casi todo routeado
    [Micromouse-kicad.kicad_pcb, Micromouse-kicad.kicad_sch]
2022-12-27 PCB Completa - Depurada
    [Micromouse-kicad.kicad_pcb, Micromouse-kicad.kicad_sch]
2022-12-27 Arreglo silkscreen
    [Micromouse-kicad.kicad_pcb]
2022-12-27 Gerber generados
    [Micromouse-kicad-B_Cu.gbl, Micromouse-kicad-B_Mask.gbs, Micromouse-kicad-B_Paste.gbp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]
2022-12-27 BOM provisional
    [Micromouse-BOM.csv, Micromouse-BOM.xlsx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]
2022-12-27 Primera iteración finalizada
    [Micromouse-kicad-B_Cu.gbl, Micromouse-kicad-B_Mask.gbs, Micromouse-kicad-B_Paste.gbp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]
2022-12-27 Modelo 3D
    [Micromouse-kicad.kicad_pcb, Micromouse-kicad.kicad_sch]
2022-12-27 Sensor IR Modelado
    [Micromouse-kicad.kicad_pcb]
2022-12-27 Ajuste VL180X
    [Micromouse-kicad.kicad_pcb]
2023-06-08 arreglo módulo frontal
    [Micromouse-kicad.kicad_pcb]
2023-06-08 arreglo conector potencia
    [Micromouse-BOM.xlsx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]
2023-06-08 Componentes listos
    [Micromouse-BOM.xlsx]
2023-06-08 Arreglos pines stm32
    [Micromouse-kicad.kicad_pcb, Micromouse-kicad.kicad_sch]
2023-06-11 modelos actualizados
    [10118193-0001LF--3DModel-STEP-56544.STEP, HC_05 Blue Tooth Module.stp, Micromouse-kicad.kicad_pcb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]
2023-06-11 Modelo 3D listo
    [DRV8833PW.STEP, LEDcASE.step, MPU-6500--3DModel-STEP-1.STEP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]
2023-06-18 It1 FloodFill: Llega con éxito a la meta
2023-08-03 modelos 3D en Kicad
    [Micromouse-kicad.kicad_pcb, MiniSumo_wheel.STP, Urethane_Sumo_Wheel.IGS.STP]
2023-08-03 Pruebas de control inicial motores

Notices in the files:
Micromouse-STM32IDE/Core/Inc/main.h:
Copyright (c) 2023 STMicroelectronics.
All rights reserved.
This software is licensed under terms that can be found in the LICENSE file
